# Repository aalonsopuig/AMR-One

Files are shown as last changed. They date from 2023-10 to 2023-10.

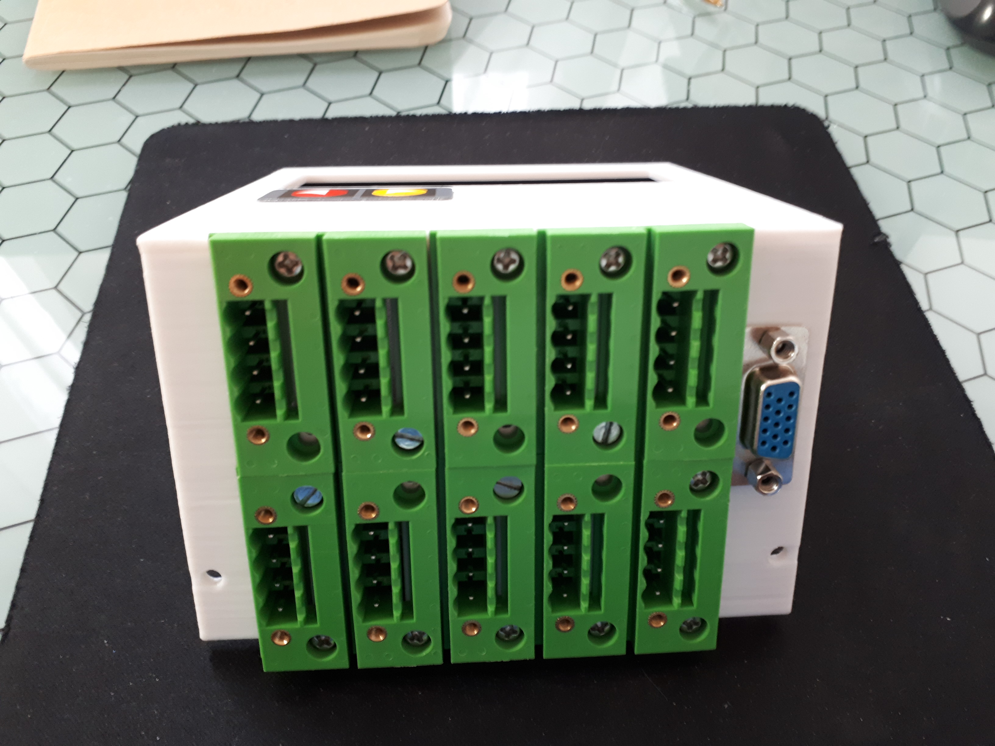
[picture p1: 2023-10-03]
amr_one_media/IMG_20210604_084052.jpg

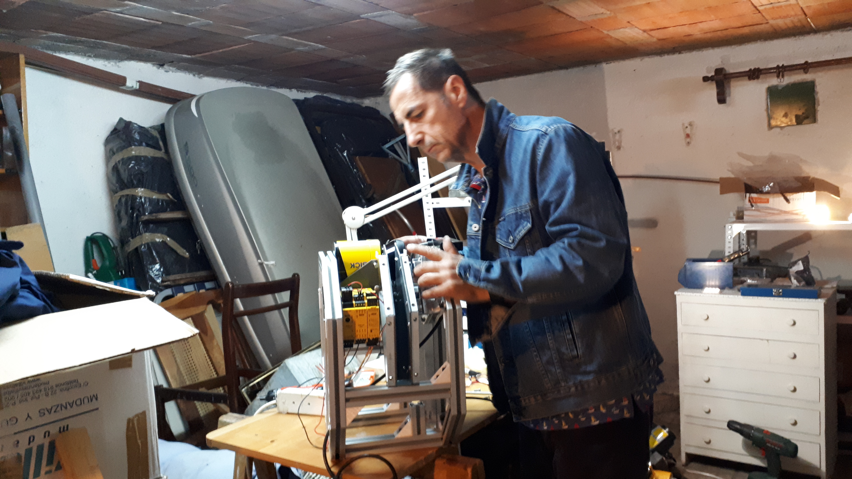
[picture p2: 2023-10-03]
amr_one_media/20200813_082543.jpg

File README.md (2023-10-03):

# AMR-One
 [C++, Python, ROS, Gcode] 2022. Autonomous Mobile Robot<br>

_Status [3/10/2023]: Done: The mechanical and electric parts of the robot, the magnetic navigation, the safety systems, and the cloud monitoring are fully operational. Pending: ROS SLAM-based navigation_
 <br><br>

## Summary of the project

The AMR-One project objective is to develop a prototype of an autonomous mobile robot for the industry, as a personal project, with some basic characteristics:<br><br>
IMG-20200915-WA0002
<br><br>
- Rotational base with damped traction system<br>
- Safety system<br>
- Pinhook system to hook trolleys from the bottom and carry them.<br>
- Two navigation modes:<br>
    * Magnetic band guidance with RFID tags control<br>
    * SLAM based navigation using ROS<br>
- Cloud monitoring (over AWS)<br><br>

## Repository content

In this repository, you could find the following folders:<br>
<br>

- **amr_one_tech_doc**: Technical documentation of the project<br>
- **amr_one_mechanical**: CAD designs produced with [FreeCad opensource program](https://www.freecad.org/), 3D printing parts, Assembly instructions, BOM,...
- **amr_one_electric**: Electric designs produced with [QElectrotech opensource program](https://qelectrotech.org/)
- **amr_one_software**: Software for Low-Level Controller (based on Arduino). Software included (.ino), Configuration of drivers, cloud,...
- **amr_one_safety**: Safety configuration for Sick FlexySoft safety PLC and Sick safety lidar
- **amr_one_media**: Photos and videos

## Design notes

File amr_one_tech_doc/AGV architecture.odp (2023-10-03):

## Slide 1

AMR Architecture

Safety

LiDAR

HMI

WIFI radio

PC

Safety PLC

Rearm button

E.Stop button

Other sensors

PLC

Magnetic band

Drives

RFID sensor

Motors

Encoders

Batt sensor

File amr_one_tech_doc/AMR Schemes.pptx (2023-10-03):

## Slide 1

Motor1_setpoint

1

PID_output1 = PID_output1 + Motor1_PID.step(Motor1_setpoint, Motor1_feedback);

Motor1_PWM = MOTORS_PWM_STOP + PID_output1;

D

Motor1_PID.step(Motor1_setpoint, Motor1_feedback);

C

6

3

Proportional

PID_output1

Motor1_PWM

FILTER

Integral

+

+

4

+

5

PWM to Volt.

Derivative

MOTORS_PWM_STOP

A

B

DRIVE

E

2

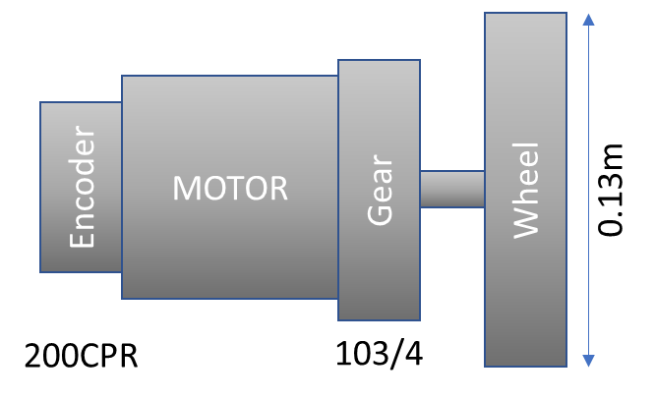
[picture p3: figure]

Motor1_feedback

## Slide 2

How 257.5 is calculated:
*
* encoder CPR: 200CPR (cycles per revolution in motor axel)
* gear ratio of motors: 103/4
* CPR_on_wheel (Resulting cycles per revolution in wheel axel): encoder CPR * gear ratio = 5150 cycles per revolution of wheel
*
* Motors_setpoint is measured in cycles of encoder per measuring time (20 miliseconds)
* period_ms = 20ms
*
* Diameter of wheel: 130mm = 13cm = 0.13m
* Perimeter_of_wheels_in_meters: Pi * Diameter = 0.4m
*
* 1 minute = 60000ms
*
* Speed_meters_per_minute = Linear_Velocity(m/s) * 60 seconds
* revolutions_per_minute = Speed_meters_per_minute / Perimeter_of_wheels_in_meters
* revolutions_per_ms = revolutions_per_minute / 60000ms
*
* Motors_setpoint = revolutions_per_ms * period_ms * CPR_on_wheel
*/

MOTOR

Encoder

Gear

Wheel

0.13m

200CPR

103/4

MOTOR

Encoder

Gear

Wheel

0.13m

200CPR

103/4

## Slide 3

MOTORS_MaxLinear_Velocity (m/s)

MOTORS_MaxAngular_Velocity x 0,836875/12.875

0

MOTORS_MaxAngular_Velocity x 0,836875/12.875

-MOTORS_MaxAngular_Velocity (rad/s)

-MOTORS_MaxLinear_Velocity (m/s)

MOTORS_MaxAngular_Velocity (rad/s)

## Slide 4

RS-232 (57.6 kBd; 8 data bits, no parity, 1 stop bit);

8C 22 0C AC xx
B9 EE F9 A9 D6

49 bits?
No empieza RS232 con high?
Debemos invertir?
Con movil da
07:46:A9:94:50:01:04:E0
Impreso: -7429-
Memoria: 1D:05

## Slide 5

RS-232 (57.6 kBd; 8 data bits, no parity, 1 stop bit);

Original Data

7.4v

0v

-8.2v

Final Data

5v

0v

Byte 1

Byte 2

Byte 3

Byte 4

Byte 5

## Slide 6

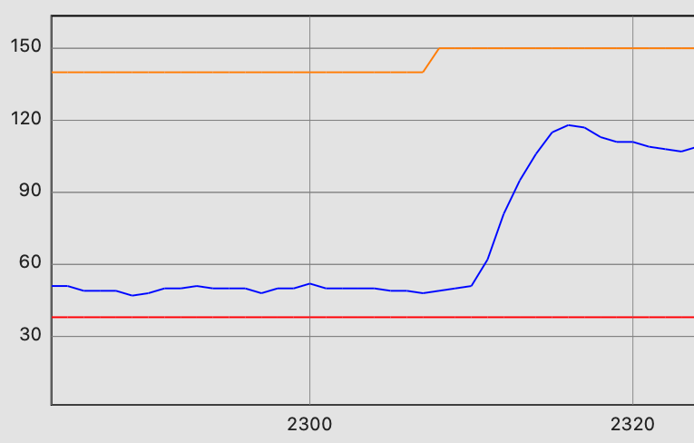
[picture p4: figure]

50ms

100ms

150ms

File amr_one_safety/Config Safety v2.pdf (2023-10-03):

# Flexi Soft Designer

# SICK

## Application name: SICK Flexi Soft main module FX3-CPU1

## Device CRC Tool: 0x3F55A961 - Device CRC Device: 0x3F55A961

## Configuration date and time: 2/8/2021 10:12:00 AM

# Flexi Soft Designer 2/8/2021 10:26:10 AM

# Content

# 1. Bill of material

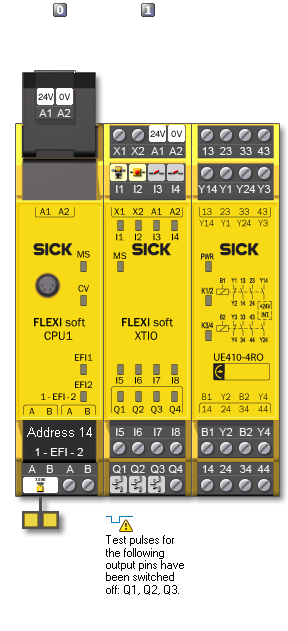
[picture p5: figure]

QTY | Title | Tag name | Part number

### Internal item number

### Description

1 | CPU1 | CPU1[0] | 1043784 | SICK Flexi Soft main module FX3-
| | | | CPU1
1 | MPL0 | System plug | 1043700 | Flexi Soft system plug
1 | S300 / Safety laser scanner, type 3 S300.CPU1
| | [0].EFI1.1 | | Sampling laser scanner for access
| | | | protection on machines, for mobile
| | | | applications as well as for vertical
| | | | access protection
1 | XTIO | XTIO[1] | 1044125 | SICK Flexi Soft expansion module
| | | | FX3-XTIO
1 | Safety switch / Single channel | Safety switch.XTIO
| | [1].I1
1 | E-Stop, ES21 / Single channel | EX-Stop.XTIO[1].I2
1 | Single channel NO / Single channel LCase1/2.XTIO[1].I3

QTY | Title | Tag name | Part number

### Internal item number

### Description

1 | Single channel NO / Single channel LCase2/2.XTIO[1].I4
1 | PNP output / Single channel | ON DRV1.XTIO
| | [1].Q1
1 | PNP output / Single channel | ON DRV2.XTIO
| | [1].Q2
1 | PNP output / Single channel | SAFETY STOP
| | ON.XTIO[1].Q3
1 | UE410-4RO3 | UE410-4RO3 | 6026143 | SICK relay output expansion
| | | | UE410-4RO3

# 2. Diagnostics

## Current operation time: 1.18:36:38, power cycle: 121 - Current: 1, Historical: 42

Time stamp | Local time | Power-up cycles Source | Code

### Description

1.18:34:07 | 2/8/2021 10:23:42 AM | 121 | Main module | 0x000F000B
Communication at EFI 1 to device address 7 interrupted: Timeout at reception of
| cyclic data. | | | [01 07 03 FFFF]
1.17:02:40 | | 120 | Extension module 1 | 0x4704
Extension module 1: cross-circuit at output Q1, 2, 3, 4 | [01 00 0F 00]
1.02:36:44 | | 104 | Extension module 1 | 0x4704
Extension module 1: cross-circuit at output Q1, 2, 4 | [01 00 0B 00]
22:55:03 | | 96 | Extension module 1 | 0x4502
Internal error: Cross-checking for inputs | [01 55 04 00]
22:55:01 | | 96 | Extension module 1 | 0x4502
Internal error: Cross-checking for inputs | [01 55 04 00]
22:54:37 | | 96 | Extension module 1 | 0x4502
Internal error: Cross-checking for inputs | [01 AA 08 00]
20:14:48 | | 80 | Extension module 1 | 0xC30A
Internal error in the Flexi Soft system. | [01 00 0F 00]
20:14:48 | | 80 | Main module | 0x0029C006
Internal error in the Flexi Soft system: Probably an extension module is
| malfunctioning. | | | [00 02 00 00]
17:51:38 | | 60 | Main module | 0x002D4006
The Flexi Soft system performed a restart due to a power supply dip at the main
| module. | | | [00 00 00 00]
14:45:52 | | 56 | Extension module 1 | 0xC30A
Internal error in the Flexi Soft system. | [01 00 0F 00]
14:45:52 | | 56 | Main module | 0x0029C006
Internal error in the Flexi Soft system: Probably an extension module is
| malfunctioning. | | | [00 02 00 00]
14:36:23 | | 46 | Main module | 0x00404006
| Force mode terminated. | | | [00 00 00 00]
14:34:12 | | 46 | Main module | 0x003F4006
| Force mode started. | | | [00 00 00 00]
14:33:44 | | 46 | Main module | 0x00404006
| Force mode terminated. | | | [00 00 00 00]
14:32:27 | | 46 | Main module | 0x003F4006
| Force mode started. | | | [00 00 00 00]
11:54:28 | | 42 | Main module | 0x00404006
| Force mode terminated. | | | [00 00 00 00]
11:52:52 | | 42 | Main module | 0x003F4006
| Force mode started. | | | [00 00 00 00]
11:05:07 | | 40 | Main module | 0x00404006
| Force mode terminated. | | | [00 00 00 00]
11:03:17 | | 40 | Main module | 0x003F4006
| Force mode started. | | | [00 00 00 00]
10:00:13 | | 39 | Main module | 0x00404006
| Force mode terminated. | | | [00 00 00 00]
09:57:58 | | 39 | Main module | 0x003F4006
| Force mode started. | | | [00 00 00 00]

Time stamp | Local time | Power-up cycles Source | Code

### Description

08:14:05 | 37 | Main module | 0x000F4013
Configuration in the system plug is incompatible for at least one extension module. [01 FFFF 00 00]
08:13:59 | 37 | Main module | 0x0019400A
Unexpected EFI device with address 7 found at EFI 1. Either remove this device or
adapt the configuration of the Flexi Soft system.

[01 07 00 00]

08:13:53 | 37 | Main module | 0x000E4006
Configuration in the system plug is invalid. | [00 00 00 01]
08:13:11 | 36 | Main module | 0x001B4005
Internal error in the Flexi Soft system. | [58E6 526D 5BF8
DB91]
07:17:20 | 28 | Main module | 0x0009400A
Communication at EFI1 interrupted. Communication driver has switched off. After
solving the fault a restart of the Flexi Soft system is necessary.

[01 422 00 00]

06:51:21 | 28 | Main module | 0x000F4013
Configuration in the system plug is incompatible for at least one extension module. [01 FFFF 00 00]
06:51:15 | 28 | Main module | 0x0019400A
Unexpected EFI device with address 7 found at EFI 1. Either remove this device or
adapt the configuration of the Flexi Soft system.

[01 07 00 00]

06:51:09 | 28 | Main module | 0x000E4006
Configuration in the system plug is invalid. | [00 00 00 01]
06:50:56 | 27 | Main module | 0x001B4005
Internal error in the Flexi Soft system. | [5DB5 A17E 5EAB
2882]
06:47:07 | 27 | Main module | 0x001B4005
Internal error in the Flexi Soft system. | [5DB5 A17E 5EAB
2882]
05:11:53 | 20 | Extension module 1 | 0x4704
Extension module 1: cross-circuit at output Q1, 2, 3, 4 | [01 00 0F 00]
04:50:54 | 18 | Main module | 0x0019400A
Unexpected EFI device with address 7 found at EFI 1. Either remove this device or
adapt the configuration of the Flexi Soft system.

[01 07 00 00]

02:15:25 | 11 | Main module | 0x0019400A
Unexpected EFI device with address 7 found at EFI 1. Either remove this device or adapt the configuration of the Flexi Soft system.

[01 07 00 00]

02:13:12 | 10 | Main module | 0x00404006
Force mode terminated. | [00 00 00 00]
02:11:32 | 10 | Main module | 0x003F4006
Force mode started. | [00 00 00 00]
02:01:45 | 10 | Main module | 0x000F4013
Configuration in the system plug is incompatible for at least one extension module. [01 FFFF 00 00]
02:01:33 | 10 | Main module | 0x000E4006
Configuration in the system plug is invalid. | [00 00 00 01]
02:01:00 | 9 | Main module | 0x000F4013
Configuration in the system plug is incompatible for at least one extension module. [01 FFFF 00 00]
02:00:48 | 9 | Main module | 0x000E4006
Configuration in the system plug is invalid. | [00 00 00 01]
01:57:38 | 8 | Main module | 0x000F4013
Configuration in the system plug is incompatible for at least one extension module. [01 FFFF 00 00]
01:57:26 | 8 | Main module | 0x000E4006
Configuration in the system plug is invalid. | [00 00 00 01]
01:55:17 | 7 | Extension module 1 | 0x4601
Extension module 1: Cross circuit at input I1 | [01 00 01 00]

# 3. Summary

# 3.1. Module 0

### Device class:

### Type code: Serial number:

### Software version

### Hardware version:

### Version/ Step:

### Operational status:

CPU1 | FX3-
CPU130002
1427 0089 | V 3.01.0 | 4.00 | 1.9.2.187 V 3.xx Online

# 3.2. Module 1

### Device class:

### Type code: Serial number:

### Software version

### Hardware version:

### Version/ Step:

### Operational status:

XTIO | FX3-XTIO84002 1632 1341 | V 3.10.0 | 1.11 | 1.9.2.187 V 3.xx Online

# 3.3. EFI 1.1 S300 [H]

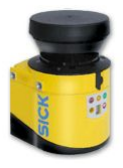
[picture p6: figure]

Device | S300 [H]
Device name | S300 LR
Type code | S30B-3011GB
Serial number | 19250478
| 15391838
Software version | 02.11
Operational status | Online

# 4. Configuration

# 4.1. Installed software components

Basic components (station) | 1.9.2.187
Software component for GCC1 Network Modules | 1.9.1.279
Software component for GS3S gateway | 1.8.0.1
Software component for UE410-2RO3 relay module | 1.9.2.187
Software component for UE410-4RO3 relay module | 1.9.2.187
Software components for Flexi-Soft FX3-ANA0 expansion module 1.9.2.187
Software component for GCAN gateway | 1.9.2.187
Software component for GDEV gateway | 1.9.2.187
Software component for GENT gateway | 1.9.2.187
Software component for GETC gateway | 1.9.2.187
Software component for GMOD gateway | 1.9.2.187
Software component for GPNT gateway | 1.9.2.187
Software component for GPRO gateway | 1.9.2.187
Software component for Drive Monitor FX3-MOC0 module | 1.9.2.187
Software component for Drive Monitor FX3-MOC1 module | 1.9.2.187
Software components for MOC3SA Motion Control module | 1.9.2.187

Software component for ReLy OSSD4 relay module | 1.9.2.187
Software component for STIO expansion module | 1.9.2.187
Software component for UE10 relay module | 1.9.2.187
Software component for UE12 relay module | 1.9.2.187
Software component for XTDI extension module | 1.9.2.187
Software components for FX3-XTDS expansion module | 1.9.2.187
Software component for XTIO extension module | 1.9.2.187
Software component for CPU0 and CPU1 main modules | 1.9.2.187

# 4.2. General information

User group | Authorized client
Application name | SICK Flexi Soft main module FX3-CPU1
Application description
Configuration CRC | 0x3F55A961
Device CRC | 0x3F55A961
Configuration state | Verified
Device state | Verified
Configuration date | 2/8/2021 10:12 AM

Module | Type code | Step | Address
CPU1 | FX3-CPU130002 | V 3.xx | 0
XTIO | FX3-XTIO84002 | V 3.xx | 1
UE410-4RO3 | UE410-4RO3 | -

# 4.3. CPU

## 4.3.1. CPU1 - General information

### Type code Serial number

| Software
| version | Hardware
| | version | Version/Step Memory
| | | usage (UI/
| | | Logic)

### Address

FX3-CPU130002 1427 0089 | V 3.01.0 | 4.00 | 1.9.2.187 V 3.xx 6.14% / 6.01% | 0
FX3-MPL000001 1435 0415 | - | - | 1.9.2.187 | - | -
S30B-3011GB | - | - | - | - | - | EFI1.1

## 4.3.1.1. CRC values

### Project CRC value

### Device CRC value

Configuration CRC | 0x3F55A961 | 0x3F55A961

## 4.3.2. CPU logic

### Used

Function blocks | 15
Execution time (ms) | 4

## 4.3.2.1. 0-Inputs

No Name | Input | Output | Settings
0 | Routing N:N I.0 LCase1/2.XTIO[1].I3 | O.0 Routing 1:N 0 -> I.0 ->
Input
| | | | Input 1: Not Inverted
| | I.1 LCase2/2.XTIO[1].I4 | O.1 Routing 1:N 2 -> I.0 ->
Input
| | | | Input 2: Not Inverted
| | I.2 EX-Stop.XTIO[1].I2 | O.2 Routing N:N 0 -> I.2 ->
Input 3
| | | | Input 3: Inverted
5 | Routing N:N I.0 Protective field free
| | [SF].CPU1[0].EFI1.1 | O.0 Routing N:N 0 -> I.0 ->
Input 1
| | | | Input 1: Inverted
6 | Emergency
stop | | I.0 Safety switch.XTIO
[1].I1
| | | O.0 Routing N:N 0 -> I.1 ->
Input 2

Inputs: Single channel

Discrepancy time: 30 ms
Mode: Emergency stop

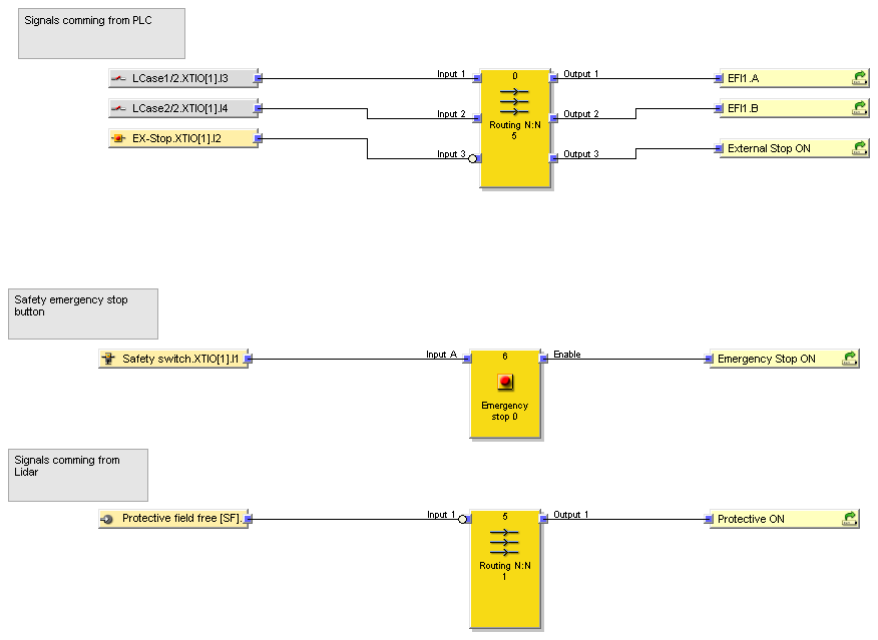
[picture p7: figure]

## 4.3.2.2. Outputs

No Name | Input | Output | Settings
1 | Routing 1:N I.0 Routing N:N 5 -> O.0 ->
| Output 1 | O.0 Input A2 [In A2].CPU1 [0].EFI1.1 O.1 NOT 0 -> I.0 -> Input
2 | NOT | I.0 Routing 1:N 0 -> O.1 ->
| Output 2 | O.0 Input A1 [In A1].CPU1 [0].EFI1.1
3 | Routing 1:N I.0 Routing N:N 5 -> O.1 ->
| Output 2 | O.0 Input B2 [In B2].CPU1 [0].EFI1.1 O.1 NOT 1 -> I.0 -> Input
4 | NOT | I.0 Routing 1:N 2 -> O.1 ->
| Output 2 | O.0 Input B1 [In B1].CPU1 [0].EFI1.1
7 | Routing N:N I.0 Routing N:N 1 -> O.0 ->
| Output 1

O.0 OR 0 -> I.0 -> Input 1 Input 1: Not Inverted

| I.1 Emergency stop 0 -> O. 0 -> Enable

O.1 OR 0 -> I.1 -> Input 2 Input 2: Not Inverted

| I.2 Routing N:N 5 -> O.2 -> Output 3

O.2 OR 1 -> I.1 -> Input 2 Input 3: Not Inverted

8 | OR | I.0 Routing N:N 0 -> O.0 ->
| Output 1 | O.0 Off delay timer 0 -> I.0 -> Input | Input 1: Not Inverted
| I.1 Routing N:N 0 -> O.1 -> Output 2 | | Input 2: Not Inverted
9 | Off delay
timer

I.0 OR 0 -> O.0 -> Output 1 O.0 Routing 1:N 3 -> I.0 ->

| | Input | Delay time: 2000 ms
10 | Routing 1:N I.0 Off delay timer 0 -> O.0
| -> Enable | O.0 SAFETY STOP ON.XTIO[1].Q3 O.1 OR 1 -> I.0 -> Input 1
11 | OR | I.0 Routing 1:N 3 -> O.1 ->
| Output 2 | O.0 Routing 1:N 1 -> I.0 -> Input | Input 1: Not Inverted
| I.1 Routing N:N 0 -> O.2 -> Output 3 | | Input 2: Not Inverted
12 | Routing 1:N I.0 OR 1 -> O.0 -> Output 1 O.0 NOT 2 -> I.0 -> Input
| | O.1 NOT 3 -> I.0 -> Input
13 | NOT | I.0 Routing 1:N 1 -> O.0 ->
| Output 1 | O.0 ON DRV1.XTIO[1].Q1
14 | NOT | I.0 Routing 1:N 1 -> O.1 ->
| Output 2 | O.0 ON DRV2.XTIO[1].Q2

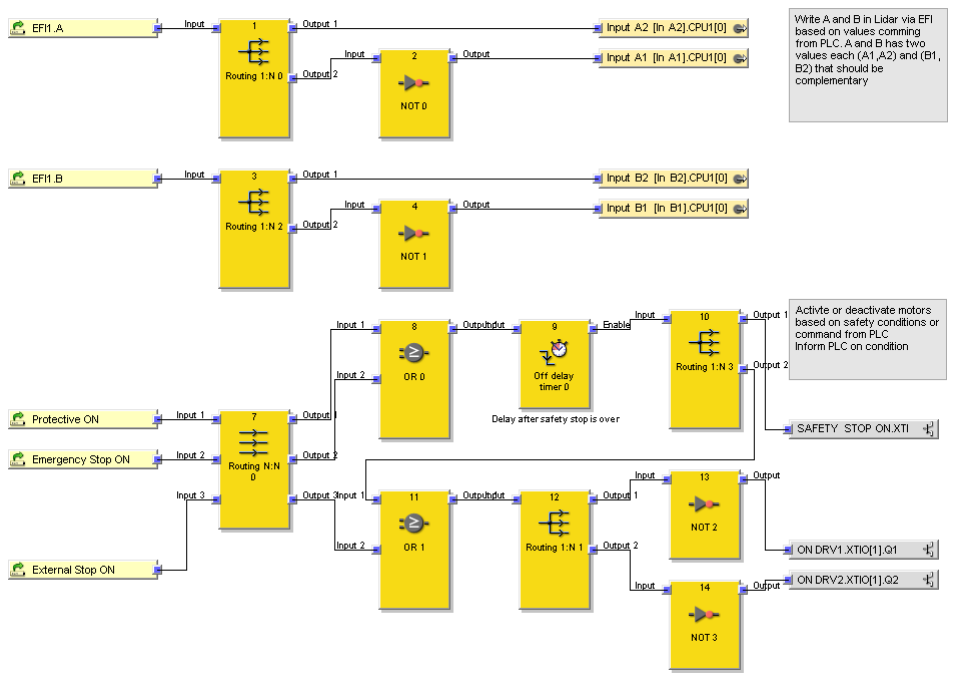
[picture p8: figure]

## 4.3.3. CPU1 - IO

Tag name | System integrity

### test based on type key

### System integrity test based on serial number

### System integrity test based on configuration date

24V | A1 | CPU1[0] Power supply
0V | A2
EFI1.1 S300.CPU1[0].EFI1.1

## 4.3.3.1. Wiring diagram

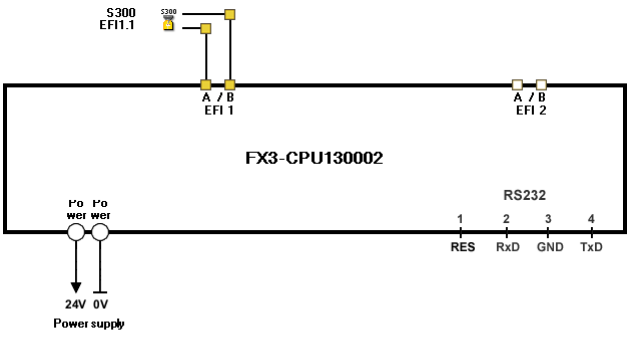
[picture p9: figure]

# 4.4. I/O module

## 4.4.1. XTIO[1]

## 4.4.1.1. General information

### Type code Serial number

### Software version

### Hardware version

### Version/Step Address

FX3-XTIO84002 1632 1341 | V 3.10.0 | 1.11 | 1.9.2.187 V 3.xx 1

## 4.4.1.2. Inputs

Mode | Title/tag name | ON-

### OFF

### OFF-

ON

### Filter time

[ms]

Dis.
[ms]

### Test period

[ms]

### Test gap

[ms]

### Max. off-on delay

[ms]
2 | 24V | I1 | Safety switch (Single
channel)
8 | – | – | – | –
3 | 24V | I2 | E-Stop, ES21 (Single
channel) / EX-Stop
0 | – | – | – | –

Mode | Title/tag name | ON-

### OFF

### OFF-

ON

### Filter time

[ms]

Dis.
[ms]

### Test period

[ms]

### Test gap

[ms]

### Max. off-on delay

[ms]
4 | 24V | I3 | Single channel NO (Single
channel) / LCase1/2
0 | – | – | – | –
5 | 24V | I4 | Single channel NO (Single
channel) / LCase2/2
0 | – | – | – | –

## 4.4.1.3. Outputs

Mode | Title/tag name | Test

### pulse

### Increase

d

### capaciti ve loads

6 | Q1 | PNP output (Single channel) / ON DRV1 | Without | Disabled
7 | Q2 | PNP output (Single channel) / ON DRV2 | Without | Disabled
8 | Q3 | PNP output (Single channel) / SAFETY STOP ON | Without | Disabled

## 4.4.1.4. Power supply

### Title/tag name

1 24V
0V

A1
A2

XTIO[1] Power supply

## 4.4.1.5. Wiring diagram

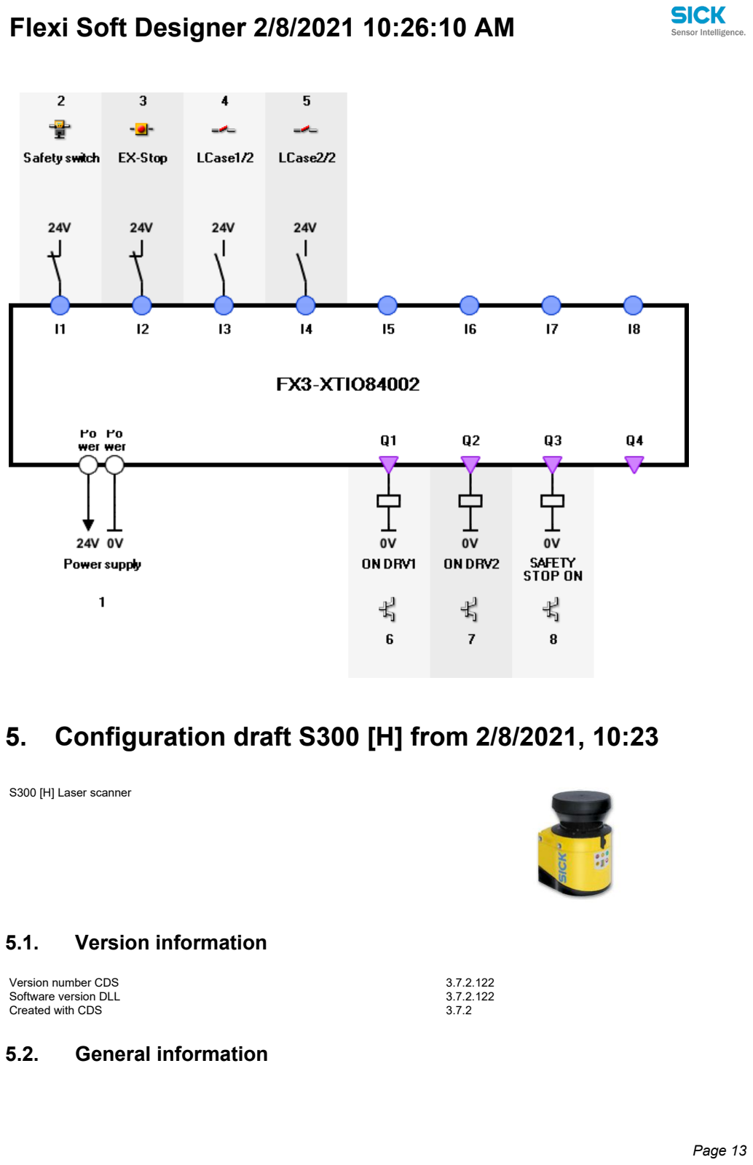
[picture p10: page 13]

# 5. Configuration draft S300 [H] from 2/8/2021, 10:23

S300 [H] Laser scanner

# 5.1. Version information

Version number CDS | 3.7.2.122
Software version DLL | 3.7.2.122
Created with CDS | 3.7.2

# 5.2. General information

Type code | S30B-3011GB
Device name | S300 LR
Serial number | 19250478
Serial number (Scanner) | 19250478
Serial number (System plug) | 15391838
Software version (CPU A) | 02.11
Software version (CPU B) | 02.11
Sensor head | Long Range (3.0 m)
I/O module
Safety Configuration ID (SCID) | 0x9C90
Status | checked

# 5.3. System parameters

Name of the user | AAP
Application name | None
Rotation of the 7segment display | Rotated by 180°

# 5.4. Resolution/scanning range

Application variant | Mobile
Resolution protective field | 70 mm (leg detection)
Basic response time | 80 ms
Maximum protective field range | 300 cm
Angular resolution | 0.5 °

# 5.5. Incremental encoder

Signal velocities | Inactive

# 5.6. Inputs

## Control inputs (Permanently)

Input source | CPU1
Input delay | 10 ms
Sampling for the static control inputs | Complementary
A | Active
B | Active
C | Inactive
D | Inactive
E | Inactive

# 5.7. OSSDs

Object in the protective field switches OSSDs | Local
External device monitoring | Inactive

# 5.8. Restart

Restart internal OSSDs | Delay by 2 s

# 5.9. Universal I/O

### Uni I/O 1 (Pin5)

### Uni I/O 2 (Pin6)

### Uni I/O 3 (Pin13)

### Uni I/O 4 (Pin14)

### Uni I/O 5 (Pin15)

### Inputs

External device monitoring | - | x
Reset | x | -

### Outputs

Contamination warning | x | - | -
Contamination error | x | - | -
Reset required | - | - | -
Error | - | - | -
Protective field | - | - | x
Warning field 1 | - | x | -
Warning field 2 | - | x | -

# 5.10. Configuration of the measured data output

Baud rate | 500 kBaud
Silent Time | 5000ms
Send mode | Continuous data output
Trigger event | Inactive
Measured data output | Distance
I/O data output | Current monitoring case
Message structure | 1 message (I/O + measured data)
Measuring range(s) | Beginning [°] | End [°] | Type
Measuring range 1 | -45 | 225 | Every value

# 5.11. Cases

Number of monitoring cases | | 4

## 5.11.1. Monitoring case 1

Monitoring case name | | Short Case
Park mode | | Inactive
Allocated field set | | Short Fields
Multiple sampling | | 4

## Activation of the inputs

Control input A | Low level
Control input B | Low level
Velocity range | Inactive

## Switching sequence

Following case | Any

## 5.11.2. Monitoring case 2

Monitoring case name | Long Case
Park mode | Inactive
Allocated field set | Long Fields
Multiple sampling | 4

## Activation of the inputs

Control input A | Low level
Control input B | High level
Velocity range | Inactive

## Switching sequence

Following case | Any

## 5.11.3. Monitoring case 3

Monitoring case name | No detection
Park mode | Inactive
Allocated field set | No detection
Multiple sampling | 2

## Activation of the inputs

Control input A | High level
Control input B | High level
Velocity range | Inactive

## Switching sequence

Following case | Any

## 5.11.4. Monitoring case 4

Monitoring case name | Park mode
Park mode | Active

## Activation of the inputs

Control input A | High level
Control input B | Low level
Velocity range | Inactive

## Switching sequence

Following case | Any

# 5.12. Field sets

Number of field sets | 3

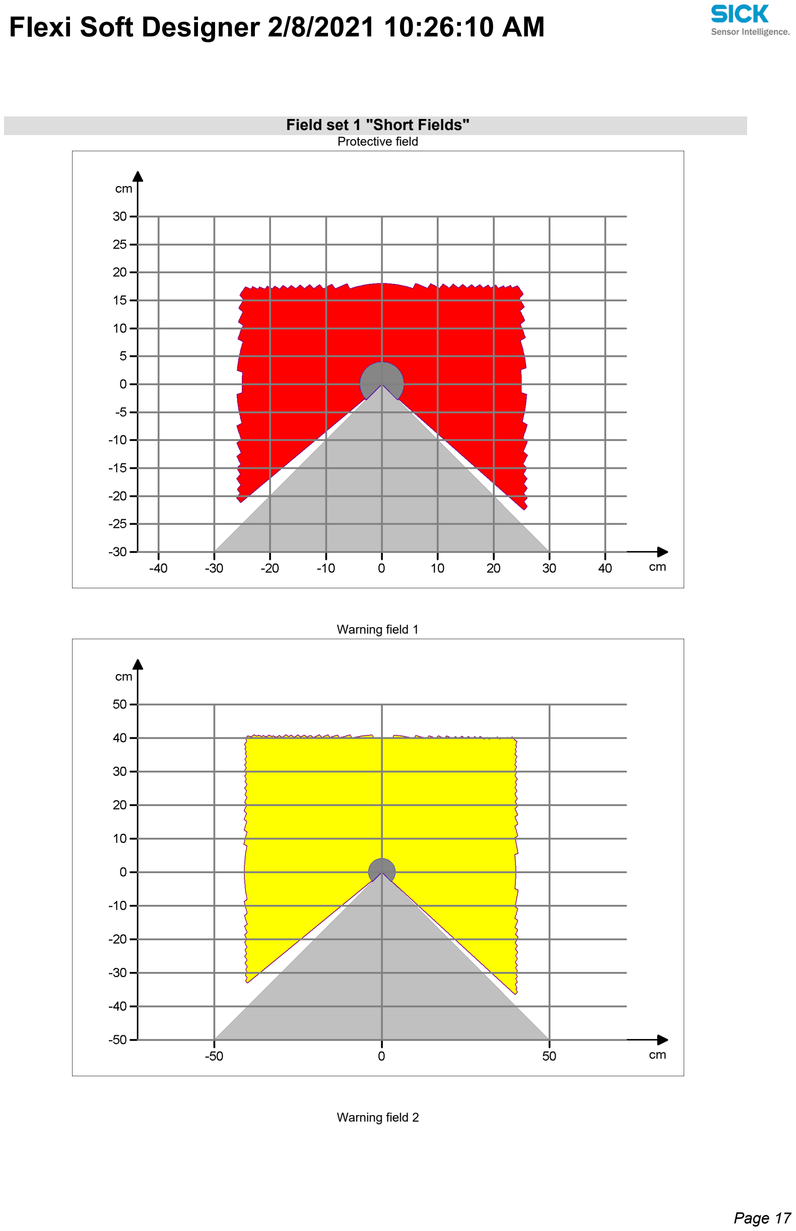
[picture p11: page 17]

### Field set 1 "Short Fields"

Protective field

Warning field 1

Warning field 2

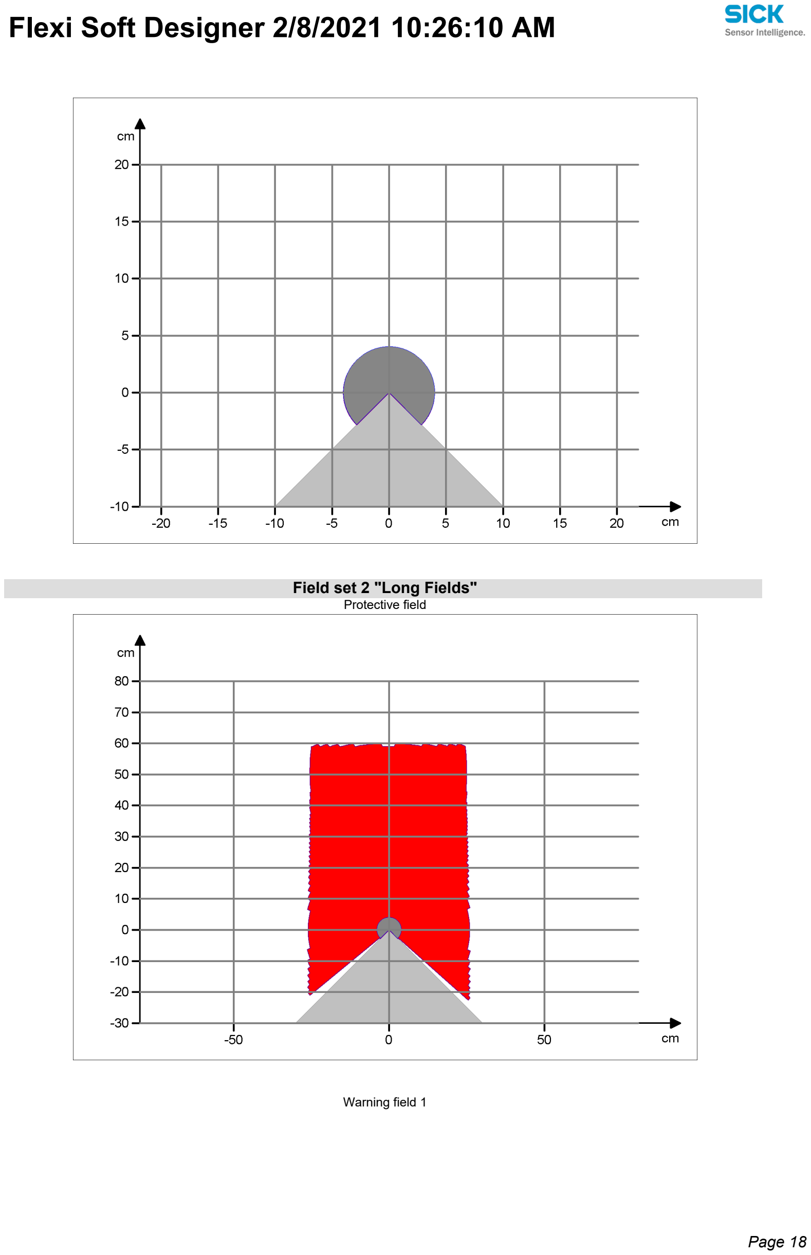
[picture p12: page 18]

### Field set 2 "Long Fields"

Protective field

Warning field 1

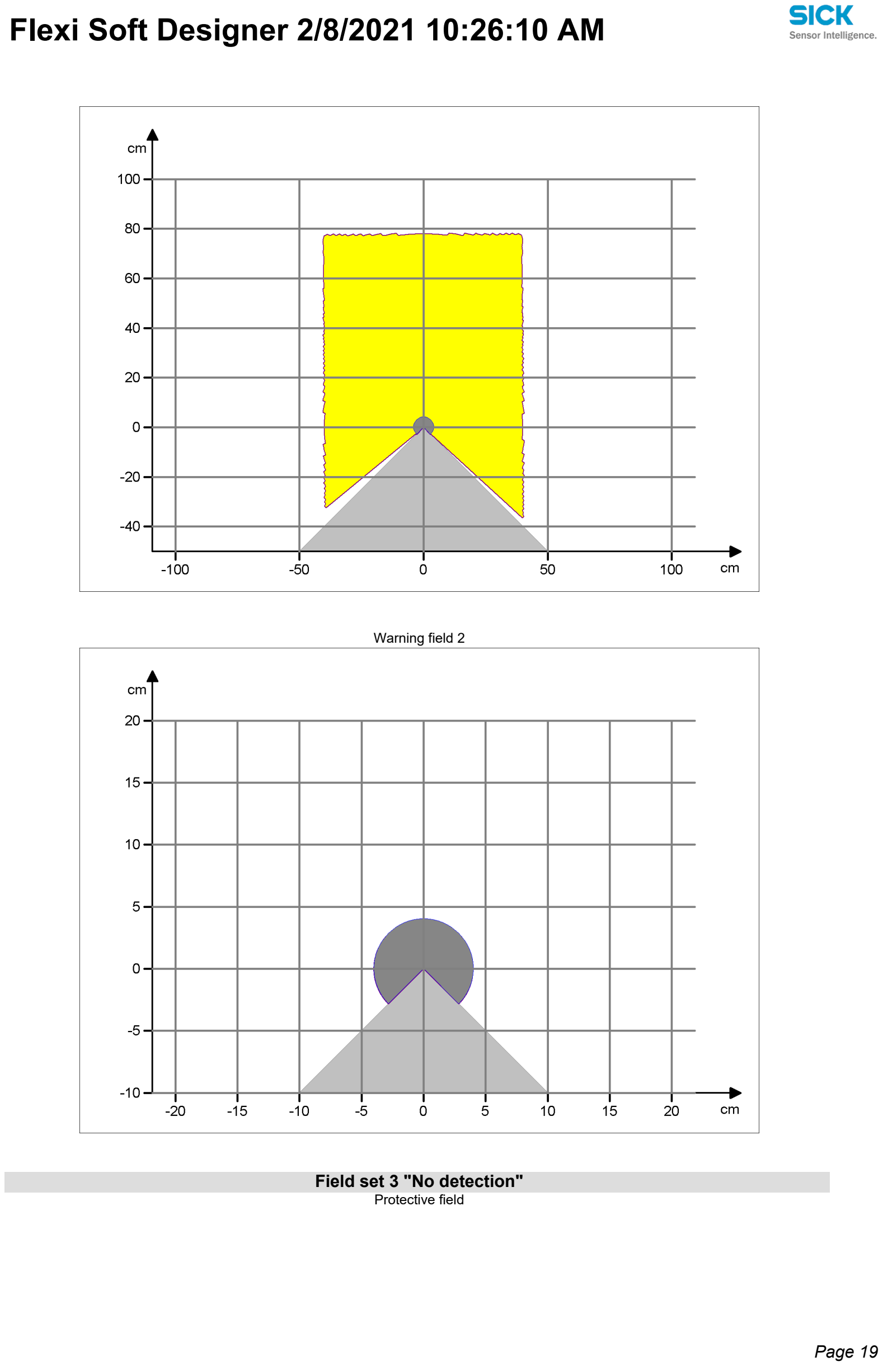
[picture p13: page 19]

Warning field 2

### Field set 3 "No detection"

Protective field

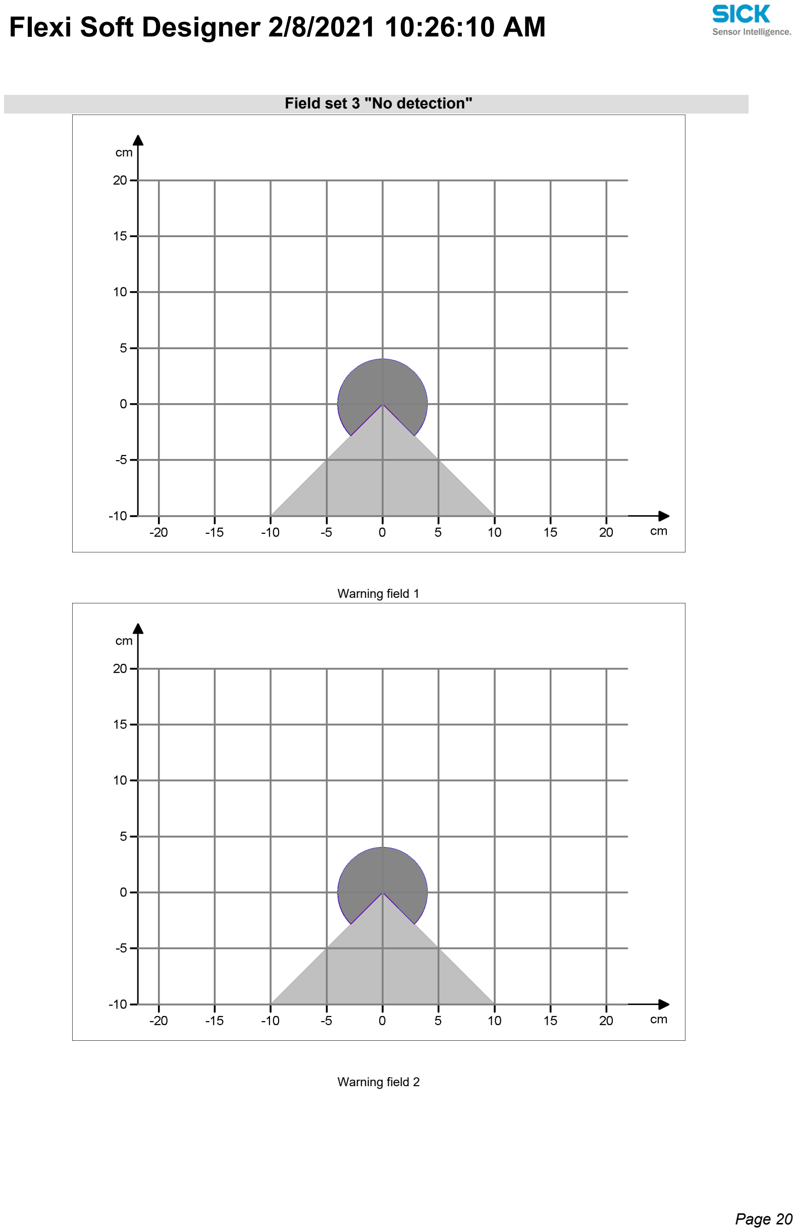
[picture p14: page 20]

### Field set 3 "No detection"

Warning field 1

Warning field 2

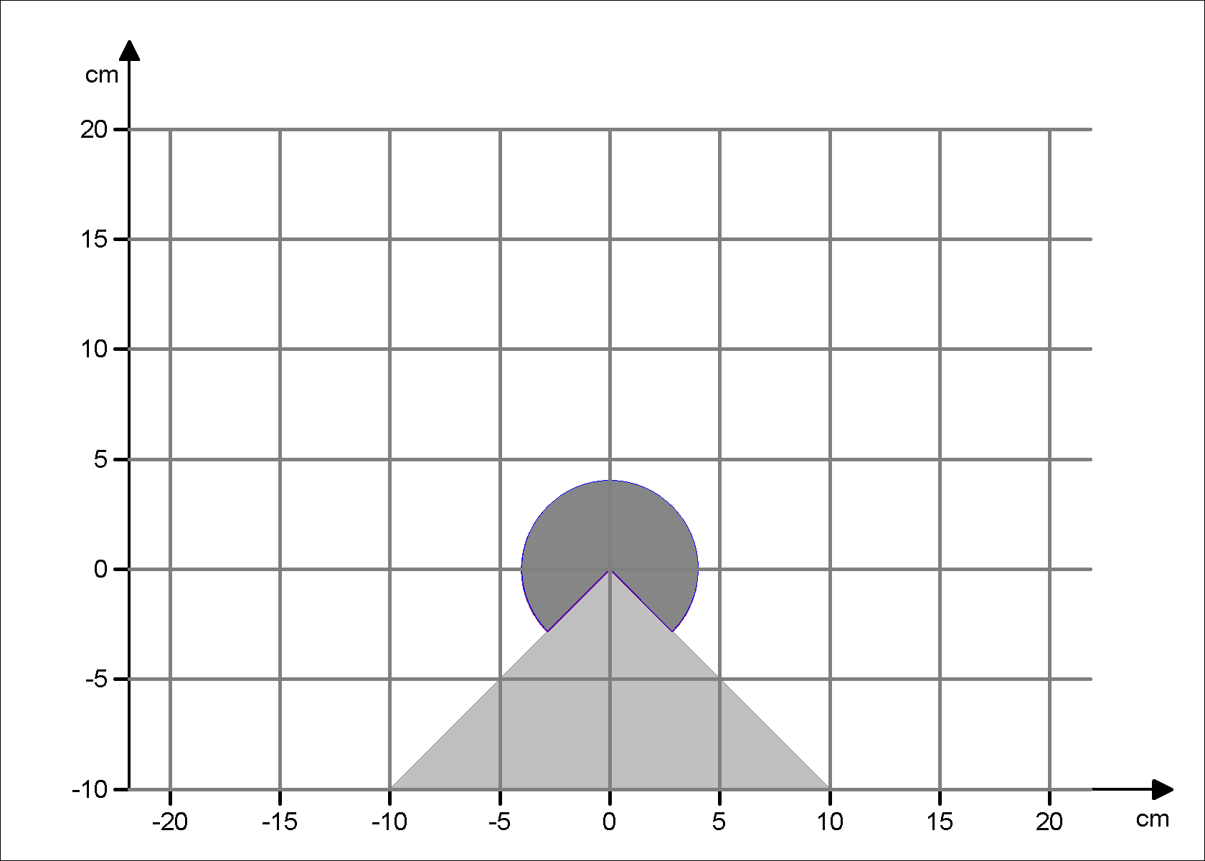
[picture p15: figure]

# 6. I/O overview

# 6.1. I/O module

XTIO[1] | Safety
switch.XTIO
[1].I1
0-Inputs | FB6 Emergency stop Input A

ON
DRV1.XTIO
[1].Q1
Outputs | FB13 NOT Output

EX-Stop.XTIO
[1].I2
0-Inputs | FB0 Routing N:N Input 3

ON
DRV2.XTIO
[1].Q2
Outputs | FB14 NOT Output

LCase1/2.XTI
O[1].I3
0-Inputs | FB0 Routing N:N Input 1

SAFETY
STOP
ON.XTIO
[1].Q3
Outputs | FB10 Routing 1:N Output 1

LCase2/2.XTI
O[1].I4
0-Inputs | FB0 Routing N:N Input 2

S300 [H]
[EFI1.1]

Input A1 [In
A1].CPU1
[0].EFI1.1
Outputs | FB2 NOT Output

Input A2 [In
A2].CPU1
[0].EFI1.1
Outputs | FB1 Routing 1:N Output 1

Input B1 [In
B1].CPU1
[0].EFI1.1
Outputs | FB4 NOT Output

Input B2 [In
B2].CPU1
[0].EFI1.1
Outputs | FB3 Routing 1:N Output 1

Protective field
free [SF].CPU1
[0].EFI1.1
0-Inputs | FB5 Routing N:N Input 1

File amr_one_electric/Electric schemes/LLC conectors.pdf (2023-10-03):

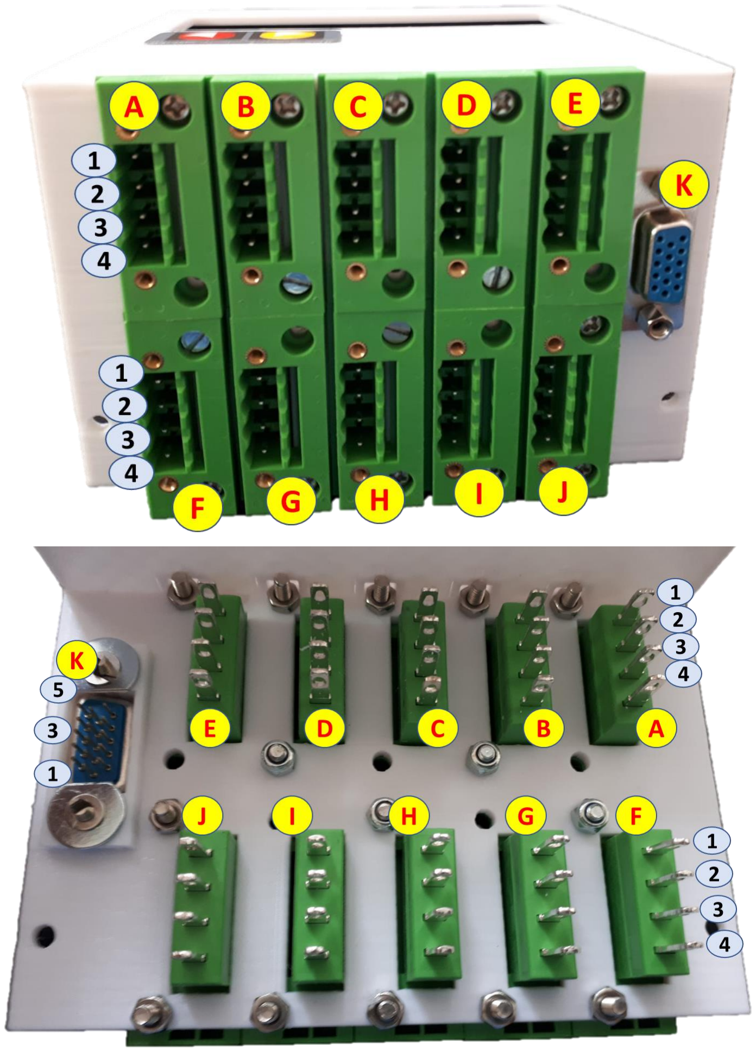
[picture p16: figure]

A. LIDAR
1. White. Lidar_Protect
2. Yellow. Lidar_Warning
3. Brown. Lidar_Dirty
4. Green. Lidar_Reset
B. Unasigned
1.
2.
3.
4.
C. SERIAL HLC
1. Black.

–LLCtrl (5v)
2. Orange. TX0

-PC
3. Gray. RX0

-PC
4.
D. Motor drive + Pinhook
1. Brown. Pinhook_a
2. White. Pinhook_b
3. Pink. Motor1_Pwm
4. Green. Motor2_Pwm
E. Button
1. Yellow. Pin_Button_Led
2. Black.

–LLCtrl (5v)
3. White. Pin_ Button
4. Red. +LLCtrl (5v)
F. POWER
1. Orange. +LLCtrl (24v)
2. Gray.

–LLCtrl (24v)
3. Red. +LLCtrl (5v)
4. Black.

–LLCtrl (5v)
G. MAG Sensor
1. Blue. MSel1
2. Yellow. MSel2
3. White. MDev
4. Brown. MGate
H. Encoder 1
1. Yellow. Encoder 1A
2. Green. Encoder 1B
3. Red. +LLCtrl (5v)
4. Black.

–LLCtrl (5v)
I. Encoder 2
1. Yellow. Encoder 1A
2. Green. Encoder 1B
3. Red. +LLCtrl (5v)
4. Black.

–LLCtrl (5v)
J. Flexi
1. Blue. SafetyStop
2. Brown. Motors_Stop
3. White. Lidar_CaseBit0
4. Yellow. Lidar_CaseBit1
K. RFID interrogator
1. Orange. +LLCtrl (24v)
3. Purple. RFID TX
5. Gray.

–LLCtrl (24v)

# LLC Connectors

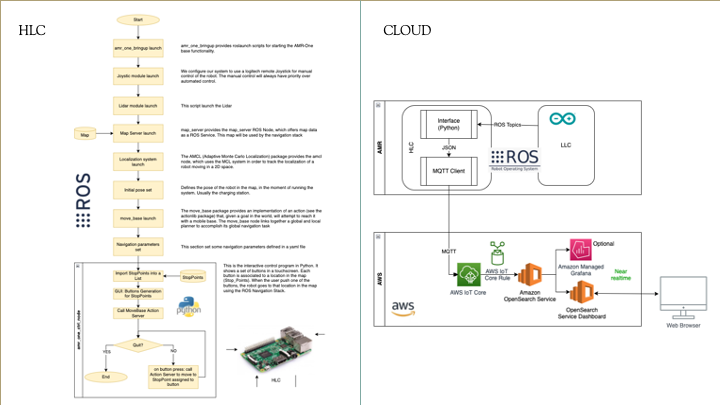
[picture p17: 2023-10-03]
amr_one_software/SW Architecture/arch_hlc_cloud.png

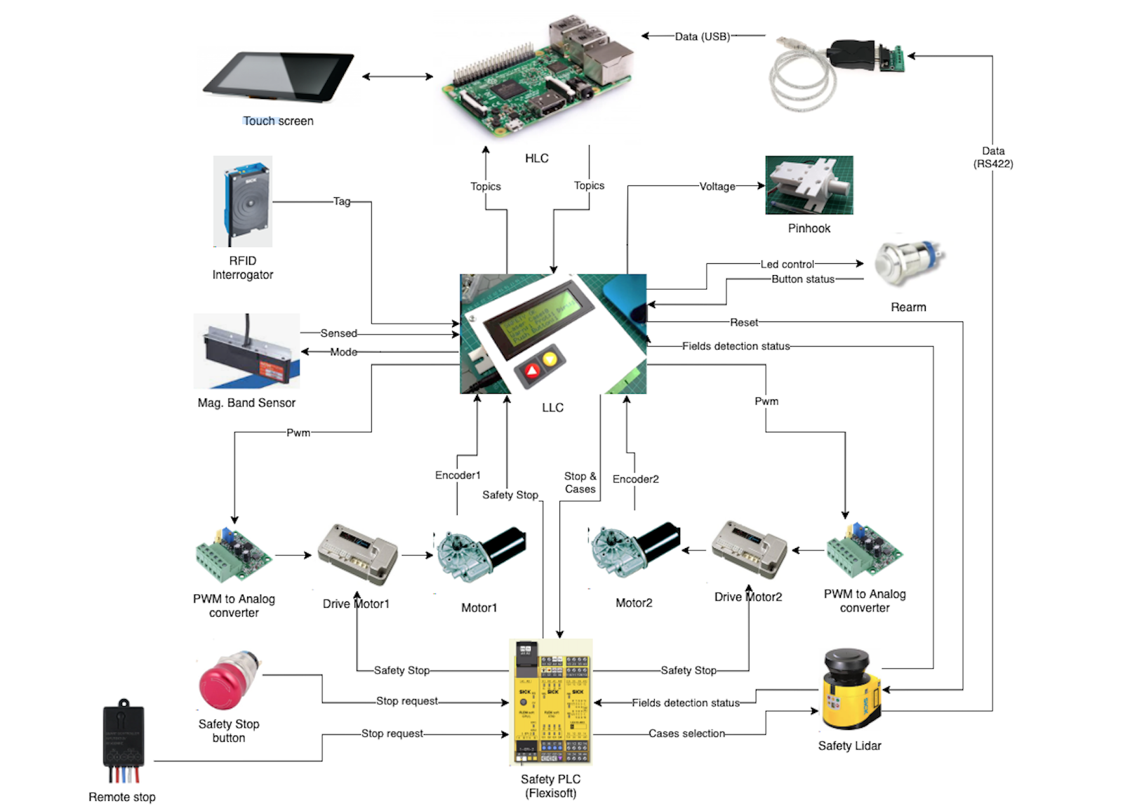
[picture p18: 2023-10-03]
amr_one_electric/HW architecture.png

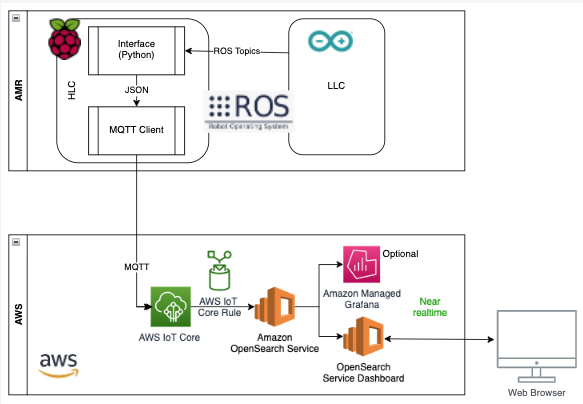
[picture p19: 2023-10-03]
amr_one_software/SW Architecture/Core Rue.png

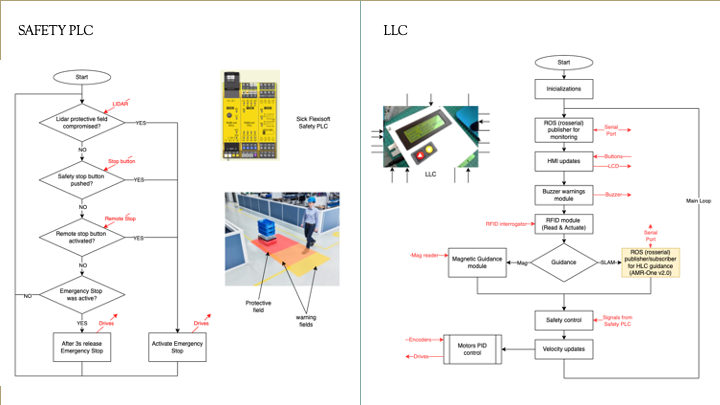
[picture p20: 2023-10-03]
amr_one_software/SW Architecture/Software.png

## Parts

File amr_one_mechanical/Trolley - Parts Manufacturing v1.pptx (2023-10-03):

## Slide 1

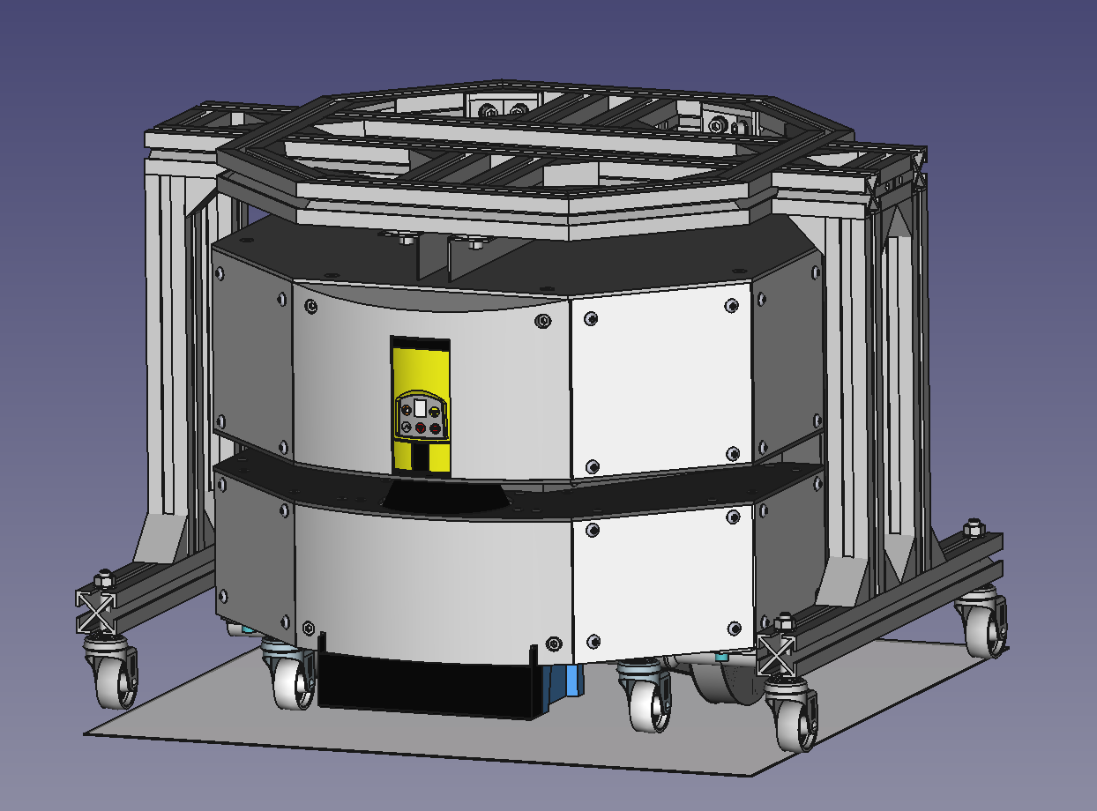
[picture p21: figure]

Trolley
Parts manufacturing

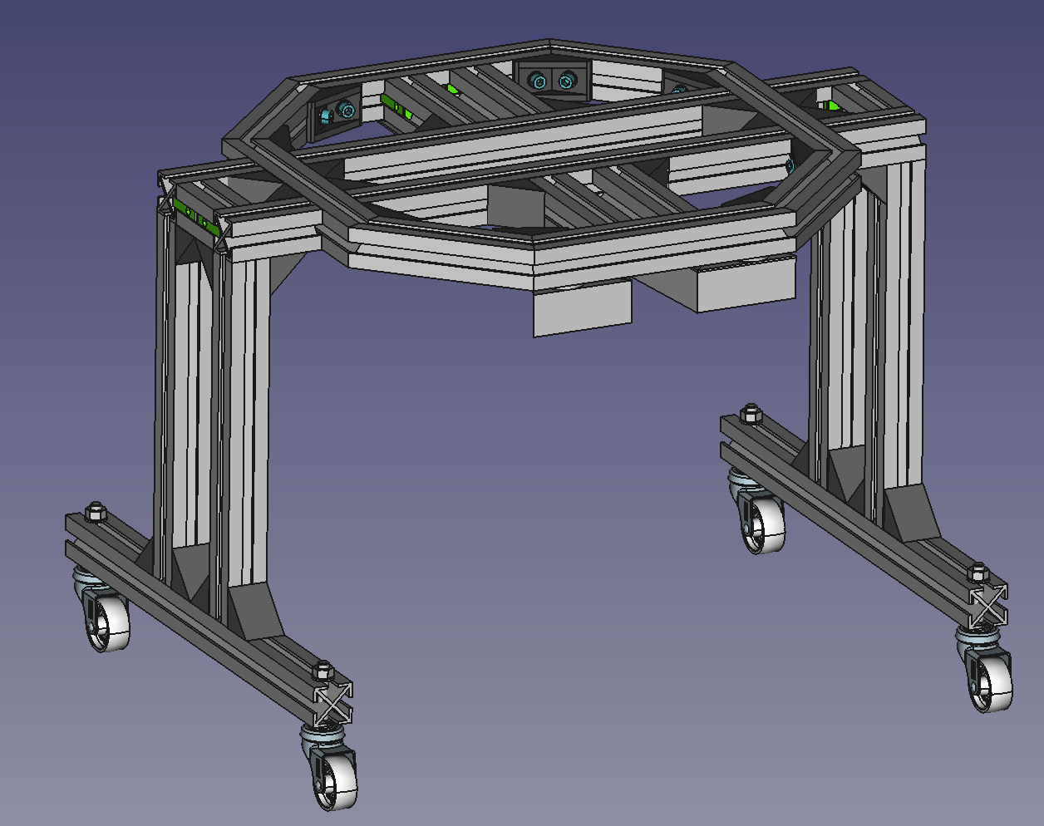
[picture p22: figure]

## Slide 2

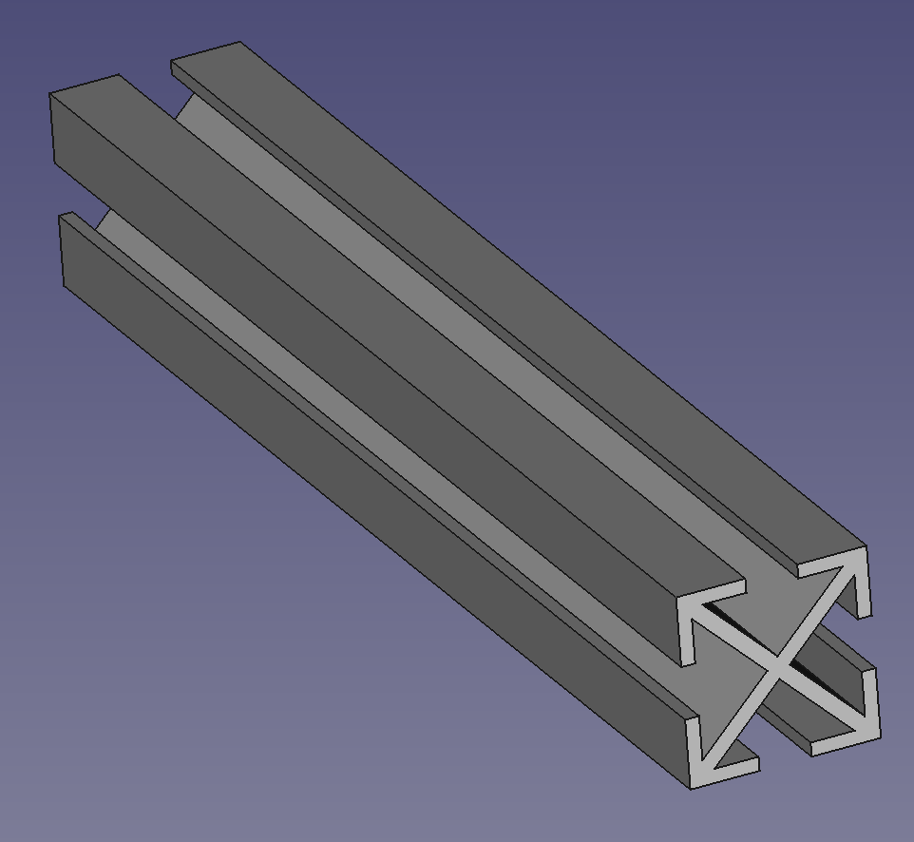
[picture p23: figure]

NOTE P176: In the each unit make two 8,2mm hole at 20mm from edge for caster wheels

P0156 | 30x30_109 mm profile flat cut | Units: 4, Assembly: Base
P0171 | 30x30_339mm profile flat cut | Units: 2, Assembly: Base
P0176 | 31x30_400mm profile flat cut | Units: 1+1, Assembly: Leg-Right, Leg-Left
P0177 | 32x30_271mm profile flat cut | Units: 2+2, Assembly: Leg-Right, Leg-Left
P0175 | 30x30_60mm profile flat cut | Units: 1+1, Assembly: LegSupport-Right / Left
P0178 | 30x30_70mm profile flat cut | Units: 2+2, Assembly: LegSupport-Right / Left

Source model for all: “30x30 profile” / 30x30 profiles.FCStd

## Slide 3

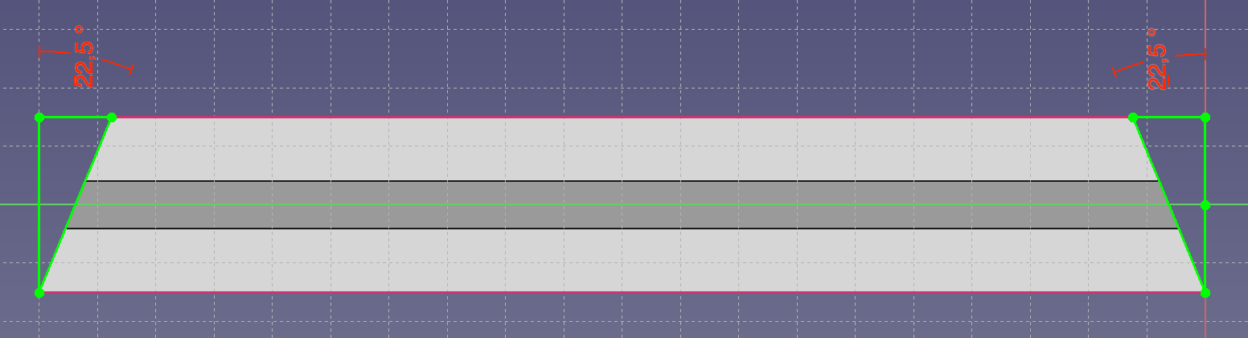
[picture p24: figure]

Length long side: 204mm
Cut angle: 22,5deg both sides
Units: 4
Assembly: Base

Length long side: 138mm
Cut angle: 22,5deg both sides
Units: 4
Assembly: Base

P0160 | 30x30 204mm profile 22,5deg cut

P0165 | 30x30 138mm profile 22,5deg cut

Source model for all: “30x30 profile” / 30x30 profiles.FCStd

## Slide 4

P0381 | Anchorage base sheet
P0391 | Steel trigger

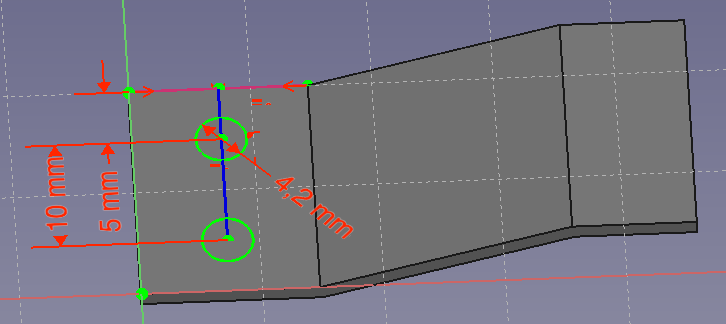
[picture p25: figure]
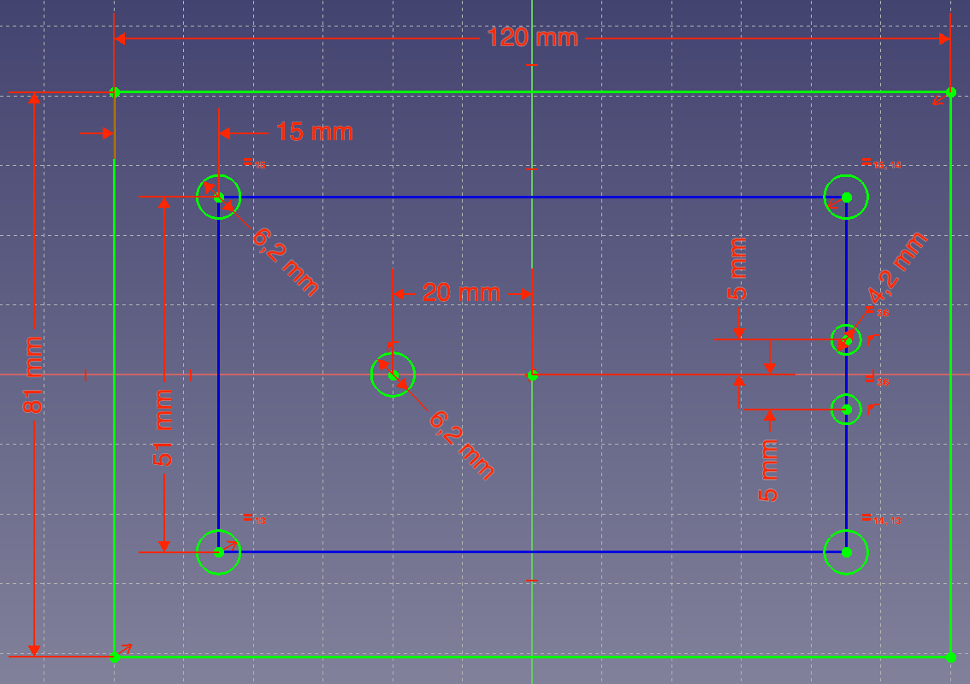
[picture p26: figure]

20mm width, 47mm length

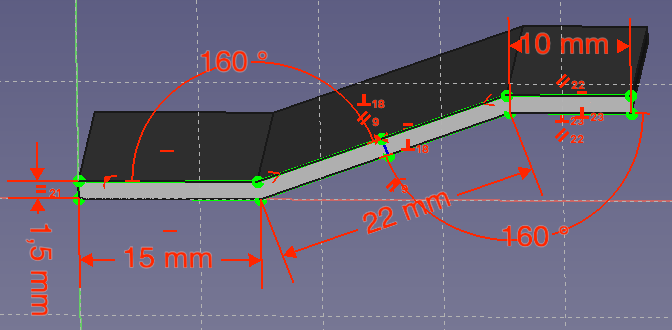
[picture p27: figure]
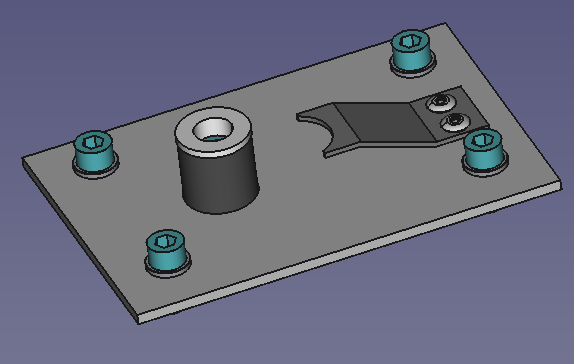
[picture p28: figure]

Source model: “Anchorage Set” / Trolley v1.3.FCStd

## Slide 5

P0206 | Aluminum Profile L shape 30x30x1,5 with rail shape R
P0207 | Aluminum Profile L shape 30x30x1,5 with rail shape L
P0382 | 3mm washer


30x30x1,5 profile, 476mm long

140mm


3mm width

77mm


Source model: “Rail Set” / Trolley v1.3.FCStd

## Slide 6

P0322 | Anchorage front limit


18mm length

Source model: “Anchorage Set” / Trolley v1.3.FCStd

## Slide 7

P0011 | 135 degree bracket

Units: 4 + 4, Printer file: 135deg bracket type 002 x8.gcode (x8 parts)
Material: PLA, Color: Gray, Weight: 63g, Printing time: 4h 18m
Assembly: Chassis Top, Chassis Bottom
Source Model: “135 degree bracket type 002” / 135 degree bracket.FCStd


P0021 | 90 degree bracket

Units: 4 + 2, Printer file: 30x30 corner bracket type 002 x6.gcode (x6 parts)
Material: PLA, Color: Gray, Weight: 48g, Printing time: 3h 26m
Assembly: Chassis Middle, Set limit motors Top
Source Model: “30x30 corner bracket type 002” / AGV-Parts v4.FCStd


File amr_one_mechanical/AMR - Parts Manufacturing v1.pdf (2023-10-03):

# AMR

## Parts manufacturing

## P0015 135deg_small_braket M6 3holes

Units: 4 + 4
Assembly: Chassis Top, Chassis Bottom

Source model: “Aluminum 30mm x 3mm flat bar” / 135degree_small_braket v2.FCStd

Length: 210mm, diameter: 16mm, wall: 0,5mm Cut angle: 90deg both sides
Units: 1
Assembly: Clutch set
P0430 | Clutch axel (tube 410x16mm)
P0435 | Balancing axel (tube 390x16mm) | Length: 210mm, diameter: 16mm, wall: 0,5mm Cut angle: 90deg both sides Units: 1 Assembly: Balancing axel set


P0390 | Clutch lever (100x5mm bar) | Length: 100mm, diameter: 5mm Cut angle: 90deg both sides Units: 1 Assembly: Clutch set



P0160 | 30x30 204mm profile 22,5deg cut
P0165 | 30x30 138mm profile 22,5deg cut
P0155 | 30x30 339 mm profile flat cut | Units: 2 + 2 Assembly: Chassis Top, Chassis Bottom
P0170 | 30x30_200mm profile flat cut
P0175 | 30x30_60mm profile flat cut | Units: 4 Assembly: Chassis Middle
| | Units: 2 Assembly: Set limit motors Top

Length long side: 204mm
Cut angle: 22,5deg both sides
Units: 4 + 4
Assembly: Chassis Top, Chassis Bottom

Length long side: 138mm
Cut angle: 22,5deg both sides
Units: 4 + 4
Assembly: Chassis Top, Chassis Bottom

Source model for all: “30x30 profile” / 30x30 profiles.FCStd

NOTE: In the 4 units for “Chassis Bottom” make an 8,2mm hole in the middle for caster wheels

## P0185 Alu Profile L shape 15x15x1,5 106mm

Length long side: 206mm
Cut angle: 90deg
Units: 1+1
Assembly: Laser beam area – Bottom, Laser beam area – Top

Source Model: “Aluminum Profile L shape type 004” / Aluminum Profiles.FCStd


## P0190 Alu Profile L shape 15x15x1,5 135mm 22,5 deg

Length long side: 135mm
Cut angle: 22,5deg both sides
Units: 2 + 2
Assembly: Laser beam area – Bottom, Laser beam area – Top

## P0195 Alu Profile L shape 15x15x1,5 137,5mm 22,5deg

Length long side: 137,5mm
Cut angle: 22,5deg both sides
Units: 2 + 2
Assembly: Laser beam area – Bottom, Laser beam area – Top

Source Model for all: “Aluminum Profile L shape type 002” / Aluminum Profiles.FCStd

NOTE: Install M5
threaded rivet as
shown

## P0200 Alu Profile L shape 15x15x1,5 197mm

Length long side: 197mm
Cut angle: 90deg both sides Units: 2
Assembly: Laser beam area – Top

Source Model: “Aluminum Profile L shape type 003” / Aluminum Profiles.FCStd

## P0205 Aluminum Profile L shape 20x20x1,5 195mm 22,5 deg

Length long side: 195mm
Cut angle: 22,5deg both sides Units: 2
Assembly: Laser beam area – Bottom

Source Model: “Aluminum Profile L shape type 005” / Aluminum Profiles.FCStd

## P0215 Alu Profile square 10x10x1 259mm with holes


Length long side: 259mm
Cut angle: 90deg both sides Units: 2
Assembly: Chassis Middle

Source Model: “Z_Alu Profile square 10x10x1 with holes” / Aluminum Profiles.FCStd

NOTE: Install M5
threaded rivet as
shown


P0220 | Aluminum Profile L shape 30x20x1,5 250mm Length long side: 250mm Cut angle: 90deg both sides Units: 2 Assembly: Batteries support
P0230 | Aluminum Profile L shape 30x20x1,5 98mm Length long side: 98mm Cut angle: 90deg both sides Units: 2 Assembly: Batteries support

Source Model for all: “Aluminum Profile L shape type 001” / Aluminum Profiles.FCStd

## P0445 DIN Rail 260mm

Length: 260mm
Cut angle: 90deg both sides
Units: 1
Assembly: Flexisoft set

NOTE: AGV_Soporte_motor_D (30mm diameter) overlaps 7mm


P0325

P0325

P0340

P0350 | P0350
P0355

P0355

P0375 | P0375

P0380a

P0380b

P0380b

P0370 | P0370 | P0345 | P0345
P0360 | P0360 | P0365 | P0365

## P0325 Laser Support

Source: Plastic sheet 3mm
Units: 2
Assembly: Laser Set

Source Model: “Laser Supports” / Laser supports.FCStd

## P0340 PVC 3mm piece: Top cover


Source Model: “Top cover” / AGV-Parts v4.FCStd

Source: Plastic sheet 3mm, 405x405mm Color: Gray
Units: 1
Assembly: Top cover set

## P0345 PVC 3mm piece: Front Side-Bottom Cover


Source Model: “Front Side-Bottom Cover” / AGV-Parts v4.FCStd

Source: Plastic sheet 3mm
Color: White
Units: 2
Assembly: Sides cover Set

## P0370 PVC 3mm piece: Front Side-Top Cover


Source Model: “Front Side-Top Cover” / AGV-Parts v4.FCStd

Source: Plastic sheet 3mm
Color: White
Units: 2
Assembly: Sides cover Set

## P0360 PVC 3mm piece: Lateral-Top Cover


Source Model: “Lateral-Top Cover” / AGV-Parts v4.FCStd

Source: Plastic sheet 3mm
Color: White
Units: 2
Assembly: Sides cover Set

## P0365 PVC 3mm piece: Lateral-Bottom Cover


Source Model: “Lateral-Bottom Cover” / AGV-Parts v4.FCStd

Source: Plastic sheet 3mm
Color: White
Units: 2
Assembly: Sides cover Set


Source Model: “Lateral-Back Cover” / AGV-Parts v4.FCStd

Source: Plastic sheet 3mm
Color: Gray
Units: 2
Assembly: Sides cover Set

## P0350 PVC 3mm piece: Lateral-Back Cover

Source Model: “Back Side Cover” / AGV-Parts v4.FCStd

Source: Plastic sheet 3mm
Color: Gray
Units: 2
Assembly: Sides cover Set

## P0355 PVC 3mm piece: Back Side Cover

## P0375 PVC 3mm piece: laser beam area sheet

Source Model: “laser beam area sheet” / AGV-Parts v4.FCStd

Source: Plastic sheet 3mm, 261 x 405 mm
Color: Gray
Units: 1 + 1
Assembly: Laser beam area – Bottom / Laser beam area – Top

Cut all this part

## P0380 PVC 3mm piece: Inside wall (Part 1)


Source Model: “Inside wall” / AGV-Parts v4.FCStd

Source: Plastic sheet 3mm
Color: Gray
Units: 1
Assembly: Sides cover Set

NOTES:
Could be done in one long piece (530x60), or split in three: -Central part (from piece 103x60mm)
-2 Side parts (from 2 pieces 212x60mm)

## P0380 PVC 3mm piece: Inside wall (Part 2)


Source Model: “Inside wall” / AGV-Parts v4.FCStd

## P0410 Bracket front laser


Source Model: “Bracket front laser” / AGV-Parts v4.FCStd

Source: Aluminum sheet 30x1,5mm
Units: 2 + 2
Assembly: Laser beam area – Bottom / Laser beam area – Top

## P0415 Drive support


Source Model: “Drive support” / AGV-Parts v4.FCStd

Source: Aluminum sheet 20x118x1,5mm Units: 2
Assembly: Drives set

Install 2 M5 threaded rivets as shown in the picture. Each piece has the rivet in a different hole.

## P0425 Bracket RFID


Source Model: “Aluminum Profile L shape type 006” / Aluminum Profiles.FCStd

Source: Aluminum sheet 30x1,5mm Units: 2
Assembly: RFID Set
NOTE: Install M4 threaded rivet as shown (note it is in different hole in each piece)


Units: 1, Printer file: AGV_Soporte_motor_D_v1.gcode
Material: PLA, Color: Gray, Weight: 44g, Printing time: 2h 33m Assembly: Motors+Encoders
Source Model: “AGV_Soporte_motor_D” / AGV_Soporte_motor_D_v1.FCStd
P0290 | AGV_Soporte_motor_D
P0295 | AGV_Soporte_motor_I

Units: 1, Printer file: AGV_Soporte_motor_I_v4.gcode
Material: PLA, Color: Gray, Weight: 44g, Printing time: 2h 33m Assembly: Motors+Encoders
Source Model: “AGV_Soporte_motor_I” / AGV_Soporte_motor_I_v4.FCStd

## P0300 AGV_Rueda

Units: 2, Printer file: AGV_Rueda_v3.gcode
Material: PLA, Color: Gray, Weight: 44g, Printing time: 4h Assembly: Motors+Encoders
Source Model: “AGV_Rueda” / AGV_Rueda_v3.FCStd

## P0260 Axel clamp

Units: 1 + 1, Printer file: Axel clamp x2.gcode (2 units at once) Material: PLA, Color: Gray, Weight: 20g, Printing time: 1h 13m Assembly: Balancing axel set, Clutch set
Source Model: “Axel clamp” / Axel clamp.FCStd


Units: 1a & 1b, Printer file: 16mm axel corner clamp side a_b long.gcode (both in one) Material: PLA, Color: Gray, Weight: 21g, Printing time: 1h 24m
Assembly: Balancing axel set
Source Model: “16mm axel corner clamp side a long” / AGV_Clamp_eje_bal_v3.FCStd Source Model: “16mm axel corner clamp side b long” / AGV_Clamp_eje_bal_v3.FCStd
P0265 | Clutch-cam A
P0270 | Clutch-cam B
P0250 | 16mm axel corner clamp side a long
P0255 | 16mm axel corner clamp side b long

Units: 1A & 1B, Printer file: Clutch Cam A and B.gcode (both in one) Material: PLA, Color: Gray, Weight: 32g, Printing time: 1h 48m Assembly: Clutch set
Source Model: “Clutch-cam A” / Clutch Cam A and B.FCStd
Source Model: “Clutch-cam B” / Clutch Cam A and B.FCStd


Units: 1 & 1A & 1B, Printer file: Clutch axel clamps and cap.gcode (all in one) Material: PLA, Color: Gray, Weight: 14g, Printing time: 56m
Assembly: Clutch set
Source Model: “Clutch axel clamp A” / Clutch axel clamps.FCStd
Source Model: “Clutch axel clamp B” / Clutch axel clamps.FCStd Source Model: “Clutch axel cup” / Clutch axel cup.FCStd
P0275 | Clutch axel cap
P0280 | Clutch axel clamp A
P0285 | Clutch axel clamp B

Units: 4 + 4, Printer file: 135deg bracket type 002 x8.gcode (x8 parts) Material: PLA, Color: Gray, Weight: 63g, Printing time: 4h 18m Assembly: Chassis Top, Chassis Bottom
Source Model: “135 degree bracket type 002” / 135 degree bracket.FCStd


Units: 4 + 4, Printer file: 135deg_small_braket M6 3holes type 002 x8.gcode (x8 parts) Material: PLA, Color: Gray, Weight: 60g, Printing time: 4h 5m
Assembly: Chassis Top, Chassis Bottom
Source Model: “135deg_small_braket M6 3holes ” / 135degree_small_braket v2.FCStd

Units: 4 + 2, Printer file: 30x30 corner bracket type 002 x6.gcode (x6 parts) Material: PLA, Color: Gray, Weight: 48g, Printing time: 3h 26m Assembly: Chassis Middle, Set limit motors Top
Source Model: “30x30 corner bracket type 002” / AGV-Parts v4.FCStd
P0011 | 135 degree bracket
P0016 | 135deg_small_braket M6 3holes
P0021 | 90 degree bracket

Units: 2 + 2, Printer file: Bracket Front Laser type 002 x4.gcode (x4 parts) Material: PLA, Color: Gray, Weight: 11g, Printing time: 45m
Assembly: Laser beam area – Bottom / Laser beam area – Top
Source Model: “Bracket Front Laser type 002” / AGV-Parts v4.FCStd

## P0411 Bracket front laser

Units: 1, Printer file: Back top Cover v2.gcode
Material: PLA, Color: White, Weight: 107g, Printing time: 6h 33m Assembly: Back Cover Set
Source Model: “Back top Cover v2” / AGV-Parts v4.FCStd


Units: 1, Printer file: Back bottom Cover.gcode
Material: PLA, Color: White, Weight: 92g, Printing time: 5h 23m Assembly: Back Cover Set
Source Model: “Back bottom Cover” / AGV-Parts v4.FCStd


Units: 2, Printer file: RPiBox.gcode
Material: PLA, Color: White, Weight: 49g, Printing time: 3h 12m Assembly: Back Cover Set
Source Model: “RPiBox” / AGV-Parts v4.FCStd
P0315 | Back top Cover
P0320 | Back bottom Cover
P0316 | RPiBox

Units: 1, Printer file: Front Top Cover.gcode
Material: PLA, Color: White, Weight: 94g, Printing time: 5h Assembly: Front Cover Set
Source Model: “Front Top Cover” / AGV-Parts v4.FCStd

Units: 1, Printer file: Front Bottom Cover.gcode
Material: PLA, Color: White, Weight: 96g, Printing time: 4h 50m Assembly: Front Cover Set
Source Model: “Front Bottom Cover” / AGV-Parts v4.FCStd
P0305 | Front Top Cover
P0310 | Front Bottom Cover

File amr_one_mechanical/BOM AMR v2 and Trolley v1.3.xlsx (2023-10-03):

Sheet: BOM
BOM AGV
 |  |  |  |  |  |  |  |  |  |  |  |  |  |  |  |  | 1 | 1 | 1 | 2 | 5 | 3 | 3 | 3 | 3 | 4 | 4 | 4 | 4 | 2 | 2 |  | 5 | 4 | 2 | 2 | 6 | 2 | 6
 |  |  |  |  |  | Parts group |  |  |  |  |  |  |  |  |  |  | Assemblies
Ref. Code | Part | Item español | DIN | Name in CAD | File where design is | Brackets | Washers | Nuts | Screws | Profiles | 3D Printed Parts | Sheets | Other mechanical parts | Other | Price | Supplier Link | Chassis Top | Chassis Bottom | Chassis Middle | Batteries support | Flexisoft set | Set limit motors Top | Balancing axel set | Clutch set | Motors+Encoders | Laser Set | Laser beam area – Inside | Laser beam area – Bottom | Laser beam area – Top | PLC Set | Drives set | ACKSys Airlink set | Back Cover Set | Front Cover Set | Caster wheels set | Magnetic Sensor set | Top cover set | RFID Set | Sides cover Set |  | Notas
P0010 | 135 degree bracket |  |  | 135 degree bracket type 001 | 135 degree bracket | x |  |  |  |  |  |  |  |  |  | https://www.amazon.com/RUN-Aluminum-Profile-Brackets-Connectors/dp/B085VQZ66D?s=industrial | 0 | 0 |  |  |  |  |  |  |  |  |  |  |  |  |  |  |  |  |  |  |  |  |  | 0
P0011 | 135 degree bracket |  |  | 135 degree bracket type 002 | 135 degree bracket | x |  |  |  |  | x |  |  |  |  |  | 4 | 4 |  |  |  |  |  |  |  |  |  |  |  |  |  |  |  |  |  |  |  |  |  | 8
P0015 | 135deg_small_braket M6 3holes |  |  | 135deg_small_braket M6 3holes | 135degree_small_braket v2 | x |  |  |  |  |  | x |  |  |  |  | 0 | 0 |  |  |  |  |  |  |  |  |  |  |  |  |  |  |  |  |  |  |  |  |  | 0 | Made with 3cm aluminum flat bar
P0016 | 135deg_small_braket M6 3holes |  |  | 135deg_small_braket M6 3holes Type002 | 135degree_small_braket v2 | x |  |  |  |  | x |  |  |  |  |  | 4 | 4 |  |  |  |  |  |  |  |  |  |  |  |  |  |  |  |  |  |  |  |  |  | 8 | Made with 3cm aluminum flat bar
P0020 | 90 degree bracket |  |  | 3030 corner bracket.stp | AGV-Parts v4 | x |  |  |  |  |  |  |  |  | 1.00 € | https://www.amazon.com/Boeray-Bracket-Aluminum-Extrusion-Profile/dp/B01GJ34D2C?rnid=3071213011&s=industrial |  |  | 0 |  |  | 0 |  |  |  |  |  |  |  |  |  |  |  |  |  |  |  |  |  | 0
P0021 | 90 degree bracket |  |  | 30x30 corner bracket type 002 | AGV-Parts v4 | x |  |  |  |  | x |  |  |  | 1.00 € | https://www.amazon.com/Boeray-Bracket-Aluminum-Extrusion-Profile/dp/B01GJ34D2C?rnid=3071213011&s=industrial |  |  | 4 |  |  | 2 |  |  |  |  |  |  |  |  |  |  |  |  |  |  |  |  |  | 6
P0022 | 90 degree bracket (small) |  |  |  |  | x |  |  |  |  |  |  |  |  | 1.00 € | https://www.amazon.com/PZRT-Aluminum-Fastener-Standard-Extrusion/dp/B07H89R3QR
P0025 | 90 degree bracket |  |  |  |  | x |  |  |  |  |  |  |  |  |  | https://www.amazon.com/80-20-2-Hole-Inside-Bracket/dp/B001IA2LYE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 |  |  |  |  |  |  |  |  |  |  |  |  |  |  |  |  |  |  |  |  |  |  |  | 0
P0030 | 45 degree bracket |  |  |  |  | x |  |  |  |  |  |  |  |  |  | https://www.amazon.com/uxcell-Aluminum-Brackets-Profile-Connectors/dp/B07SHH11CK?s=industrial |  |  |  |  |  |  |  |  |  |  |  |  |  |  |  |  |  |  |  |  |  |  |  | 0
P0035 | Washer M6 | Arandela M6 |  | Washer M6 |  |  | x |  |  |  |  |  |  |  |  | https://www.amazon.es/gp/product/B073GQLNL2 | 8 | 8 | 12 |  | 1 | 4 | 6 | 10 | 0 | 8 | 4 |  |  |  | 2 |  |  |  |  |  |  | 2 |  | 65
P0040 | Washer M5 |  |  | Washer M5 |  |  | x |  |  |  |  |  |  |  |  |  |  |  |  |  |  |  |  |  | 2 | 4 | 0 |  |  | 6 | 4 |  |  |  |  |  |  |  |  | 16
P0045 | Washer M8 |  |  | Washer M8 |  |  | x |  |  |  |  |  |  |  |  |  |  |  |  |  |  |  |  |  |  |  |  |  |  |  |  |  |  |  | 16 |  |  |  |  | 16
P0050 | T Nut M6 3030 | Tuerca en T para perfil 3030 M6 |  | T-slot nut M6 3030 |  |  |  | x |  |  |  |  |  |  |  | https://www.amazon.es/gp/product/B075WWWTYB/ref=crt_ewc_title_srh_5?ie=UTF8&psc=1&smid=A5QX2SUPA7LK7 | 20 | 20 | 12 | 8 | 1 | 4 | 6 | 8 |  | 4 | 4 | 0 | 0 | 0 | 2 | 0 | 0 | 0 | 0 | 0 | 0 | 2 | 0 | 91
P0055 | T Nut M5 3030 | Tuerca en T para perfil 3030 M6 |  |  |  |  |  | x |  |  |  |  |  |  |  | https://www.amazon.es/gp/product/B075WV9GRD/ref=crt_ewc_img_dp_6?ie=UTF8&psc=1&smid=A5QX2SUPA7LK7 | 0 | 0 | 0 | 0 | 0 | 0 | 0 | 0 |  |  |  | 0 | 0 | 3 | 4 | 2 | 4 | 4 | 0 | 0 | 8 | 0 | 48 | 73
P0060 | ISO4032_Hex_Nut_M6 |  |  |  |  |  |  | x |  |  |  |  |  |  |  |  |  |  |  |  |  |  |  | 2 |  |  |  |  |  |  |  |  |  |  |  |  |  |  |  | 2
P0065 | ISO4032_Hex_Nut_M8 |  |  | HEX Nut M8 |  |  |  | x |  |  |  |  |  |  |  |  |  |  |  |  |  |  |  |  |  |  |  |  |  |  |  |  |  |  | 4 |  |  |  |  | 4
P0070 | 30x30 inner corner L nut |  |  |  |  |  |  | x |  |  |  |  |  |  |  | https://www.amazon.com/uxcell-Interior-Connector-Aluminum-Extrusion/dp/B07VP59DY5 |  |  | 4 |  |  |  |  |  |  |  |  |  |  |  |  |  |  |  |  |  |  |  |  | 4
P0075 | Screws for inner corner L nut |  |  |  |  |  |  | x |  |  |  |  |  |  |  | https://www.amazon.es/Inoxidable-Tornillo-Prisionero-Hexagonal-Surtido/dp/B07PKMC57C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 |  |  | 8 |  |  |  |  |  |  |  |  |  |  |  |  |  |  |  |  |  |  |  |  | 8
P0080 | Countersunk flat head Cap Screws M6 x 14 | Tornillo M6x14 cabeza plana avellanada allen | DIN7991 | Screw_M6x14_CS |  |  |  |  | x |  |  |  |  |  |  | https://www.amazon.es/Tornillo-avellanado-hexagonal-m%C3%A1quina-perno/dp/B07XF1CG8X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 | 0 | 0 |  | 8 |  |  |  |  | 6 |  |  |  |  |  |  |  |  |  |  |  |  |  |  | 14 | Para perfiles 135 grados
 | Countersunk flat head Cap Screws M6 x 12 | Tornillo M6x14 cabeza plana avellanada allen | DIN7991 | Screw_M6x12_CS |  |  |  |  | x |  |  |  |  |  |  |  |  |  |  |  |  |  |  |  |  |  |  |  |  |  |  |  |  |  |  |  |  |  |  | 0
 | Countersunk flat head Cap Screws M5 x 12 |  |  | Screw_M5x12_CS |  |  |  |  | x |  |  |  |  |  |  | https://www.amazon.es/dp/B07Y5D5MZK (https://www.amazon.es/dp/B07Y5D5MZK?spLa=ZW5jcnlwdGVkUXVhbGlmaWVyPU) |  |  |  |  |  |  |  |  |  |  | 4 |  |  |  |  |  |  |  |  |  | 8 |  | 48 | 60
 | Countersunk flat head Cap Screws M3 x 12 |  |  | Screw_M3x12_CS |  |  |  |  | x |  |  |  |  |  |  | https://www.amazon.es/S2FIX-M3-SCS-PARENT-Llave-de-vaso-hexagonal/dp/B07MCH9QSH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 |  |  |  |  |  |  |  |  |  |  |  |  |  |  |  |  | 4 |  |  |  |  |  |  | 4
P0090 | Screw_M4x12 HEX |  |  | Screw_M4x12_ISO4762 |  |  |  |  | x |  |  |  |  |  |  |  |  |  |  |  |  |  |  |  |  |  |  |  |  |  |  |  |  |  |  |  |  | 2 |  | 2
P0095 | Screw_M5x12 HEX |  |  | Screw_M5x12_ISO4762 |  |  |  |  | x |  |  |  |  |  |  |  |  |  |  |  |  |  |  |  |  | 4 |  |  |  |  |  | 2 | 4 | 4 |  |  |  |  |  | 14
P0100 | Screw_M5x14 HEX |  |  | Screw_M5x14_ISO4762 |  |  |  |  | x |  |  |  |  |  |  |  |  |  |  |  |  |  |  |  |  |  | 0 |  |  |  |  |  |  |  |  |  |  |  |  | 0
P0105 | Screw_M5x16 HEX |  |  | Screw_M5x16_ISO4762 |  |  |  |  | x |  |  |  |  |  |  |  |  |  |  |  |  |  |  |  | 2 |  |  |  |  |  |  |  |  |  |  |  |  |  |  | 2
P0110 | Screw_M5x25 HEX |  |  | Screw_M5x25_ISO4762 |  |  |  |  | x |  |  |  |  |  |  |  |  |  |  |  |  |  |  |  |  |  |  |  |  | 0 |  |  |  |  |  |  |  |  |  | 0
P0115 | Screw_M5x30 HEX |  |  | Screw_M5x30_ISO4762 |  |  |  |  | x |  |  |  |  |  |  | https://www.amazon.es/Tornillo-cil%C3%ADndrico-inoxidable-longitudes-Multicolor/dp/B082FQXXD8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 (https://www.amazon.es/Tornillo-cilíndrico-inoxidable-longitudes-Multicolor/dp/B082FQXXD8?__mk_es_ES=ÅMÅŽÕÑ&rnid=1703620031&s=tools) |  |  |  |  |  |  |  |  |  |  |  |  |  | 3 | 4 |  |  |  |  |  |  |  |  | 7
P0120 | Screw_M6x12 HEX | Tornillo M6x16 hex |  | Screw_M6x12_ISO4762 |  |  |  |  | x |  |  |  |  |  |  |  |  |  |  |  |  |  |  |  |  |  |  |  |  |  |  |  |  |  |  |  |  | 0 |  | 0
P0125 | Screw_M6x14 HEX | Tornillo M6x16 hex |  | Screw_M6x14_ISO4762 |  |  |  |  | x |  |  |  |  |  |  | https://www.amazon.es/Xiedeai-Carbono-Hexagonales-Tornillo-Cabeza/dp/B07RMXVH98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 | 20 | 20 | 8 |  | 1 | 4 | 6 | 6 | 0 | 4 | 4 |  |  |  | 2 |  |  |  |  |  |  | 2 |  | 77
P0130 | Screw_M6x16 HEX | Tornillo M6x16 hex |  | Screw_M6x16_ISO4762 |  |  |  |  | x |  |  |  |  |  |  |  | 0 | 0 | 0 |  | 0 | 0 | 0 | 0 | 0 | 0 |  |  |  |  |  |  |  |  |  |  |  |  |  | 0
P0135 | Screw_M6x20 HEX |  |  | Screw_M6x20_ISO4762 |  |  |  |  | x |  |  |  |  |  |  | https://www.amazon.es/Tornillos-Sujetadores-Reborde-Inoxidable-Hexagonal/dp/B0746CFPZ8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 |  |  | 4 |  |  |  |  |  |  |  |  |  |  |  |  |  |  |  |  |  |  |  |  | 4
P0140 | Screw_M6x35 HEX |  |  | Screw_M6x35_ISO4762 |  |  |  |  | x |  |  |  |  |  |  | https://www.amazon.es/hexagonal-Socket-Pernos-tornillo-20-unidades/dp/B084RMFYZG |  |  |  |  |  |  |  | 2 |  |  |  |  |  |  |  |  |  |  |  |  |  |  |  | 2
 | M3x5 button hex screw |  |  | M3x5 BHCS |  |  |  |  | x |  |  |  |  |  |  |  |  |  |  |  |  |  |  |  |  |  |  |  |  |  |  |  | 4 |  |  |  |  |  |  | 4
P0145 | M5x12 button hex screw |  |  | M5x12 BHCS |  |  |  |  | x |  |  |  |  |  |  |  |  |  |  |  |  |  |  |  |  |  |  |  |  |  |  |  | 0 | 0 |  | 2 | 0 |  |  | 2 | Make threaded holes in aluminum beam FOR MAG SENSOR
P0150 | Screw_M8x50 HEX HEAD |  |  | Bolt HEX M8x50 |  |  |  |  | x |  |  |  |  |  |  | https://www.amazon.es/Tornillos-de-cabeza-hexagonal-ISO-4017-M8x50-con-hex%C3%A1gono-externo-8-8-galvanizado-con-tuercas-ISO/dp/B086T124L8 |  |  |  |  |  |  |  |  |  |  |  |  |  |  |  |  |  |  | 4 |  |  |  |  | 4
P0155 | 30x30 339 mm profile flat cut | Perfil 30x30 339mm corte plano |  | 30x30_339mm profile | 30x30 profiles |  |  |  |  | x |  |  |  |  |  |  | 2 | 2 |  |  |  |  |  |  |  |  |  |  |  |  |  |  |  |  |  |  |  |  |  | 4
P0160 | 30x30 204mm profile 22,5deg cut | Perfil 30x30 204mm corte biselado 22,5º |  | 30x30_204mm_22.5deg profile | 30x30 profiles |  |  |  |  | x |  |  |  |  |  |  | 4 | 4 |  |  |  |  |  |  |  |  |  |  |  |  |  |  |  |  |  |  |  |  |  | 8
P0165 | 30x30 138mm profile 22,5deg cut | Perfil 30x30 138mm corte biselado 22,5º |  | 30x30_138mm_22.5deg profile | 30x30 profiles |  |  |  |  | x |  |  |  |  |  |  | 4 | 4 |  |  |  |  |  |  |  |  |  |  |  |  |  |  |  |  |  |  |  |  |  | 8
P0170 | 30x30_200mm profile flat cut |  |  | 30x30_200mm profile | 30x30 profiles |  |  |  |  | x |  |  |  |  |  |  |  |  | 4 |  |  |  |  |  |  |  |  |  |  |  |  |  |  |  |  |  |  |  |  | 4
P0175 | 30x30_60mm profile flat cut |  |  | 30x30_60mm profile | 30x30 profiles |  |  |  |  | x |  |  |  |  |  |  |  |  |  |  |  | 2 |  |  |  |  |  |  |  |  |  |  |  |  |  |  |  |  |  | 2
P0185 | Alu Profile L shape 15x15x1,5 106mm |  |  | Alu Profile L shape 15x15x1,5 106mm front_laser | Aluminum Profiles |  |  |  |  | x |  |  |  |  |  | https://www.leroymerlin.es/fp/10209941/perfil-forma-en-l-de-aluminio-lacado-lacado |  |  |  |  |  |  |  |  |  |  | 0 | 1 | 1 |  |  |  |  |  |  |  |  |  |  | 2
P0190 | Alu Profile L shape 15x15x1,5 135mm 22,5deg |  |  | Alu Profile L shape 15x15x1,5 135mm 22,5deg t-rivets | Aluminum Profiles |  |  |  |  | x |  |  |  |  |  | https://www.leroymerlin.es/fp/10209941/perfil-forma-en-l-de-aluminio-lacado-lacado |  |  |  |  |  |  |  |  |  |  |  | 2 | 2 |  |  |  |  |  |  |  |  |  |  | 4
P0195 | Alu Profile L shape 15x15x1,5 137,5mm 22,5deg |  |  | Alu Profile L shape 15x15x1,5 137,5mm 22,5deg t-rivets | Aluminum Profiles |  |  |  |  | x |  |  |  |  |  | https://www.leroymerlin.es/fp/10209941/perfil-forma-en-l-de-aluminio-lacado-lacado |  |  |  |  |  |  |  |  |  |  |  | 2 | 2 |  |  |  |  |  |  |  |  |  |  | 4
P0200 | Alu Profile L shape 15x15x1,5 197mm |  |  | Alu Profile L shape 15x15x1,5 197mm | Aluminum Profiles |  |  |  |  | x |  |  |  |  |  | https://www.leroymerlin.es/fp/10209941/perfil-forma-en-l-de-aluminio-lacado-lacado |  |  |  |  |  |  |  |  |  |  | 0 |  | 2 |  |  |  |  |  |  |  |  |  |  | 2
P0205 | Aluminum Profile L shape 20x20x1,5 195mm 22,5deg |  |  | Alu Profile L shape type005 20x20x1,5 195mm | Aluminum Profiles |  |  |  |  | x |  |  |  |  |  | https://www.leroymerlin.es/fp/529074/perfil-forma-en-l-de-aluminio-anodizado-anodizado |  |  |  |  |  |  |  |  |  |  | 0 | 2 |  |  |  |  |  |  |  |  |  |  |  | 2
P0215 | Alu Profile square 10x10x1 259mm with holes |  |  | Alu Profile square 10x10x1 259mm with holes | Aluminum Profiles |  |  |  |  | x |  |  |  |  |  | https://www.leroymerlin.es/fp/707770/perfil-forma-tubo-cuadrado-de-aluminio-en-bruto-en-bruto |  |  | 2 |  |  |  |  |  |  |  |  |  |  |  |  |  |  |  |  |  |  |  |  | 2
P0220 | Aluminum Profile L shape 30x20x1,5 250mm |  |  | Aluminum Profile L shape type 001 30x20x1,5 250mm | Aluminum Profiles |  |  |  |  | x |  |  |  |  |  | https://www.leroymerlin.es/fp/11434360/perfil-forma-en-l-de-aluminio-anodizado-anodizado |  |  |  | 2 |  |  |  |  |  |  |  |  |  |  |  |  |  |  |  |  |  |  |  | 2
P0225 | Aluminum Profile L shape 30x20x1,5 108mm |  |  | Aluminum Profile L shape type 001 30x20x1,5 108mm | Aluminum Profiles |  |  |  |  | x |  |  |  |  |  | https://www.leroymerlin.es/fp/11434360/perfil-forma-en-l-de-aluminio-anodizado-anodizado |  |  |  | 0 |  |  |  |  |  |  |  |  |  |  |  |  |  |  |  |  |  |  |  | 0
P0230 | Aluminum Profile L shape 30x20x1,5 98mm |  |  | Aluminum Profile L shape type 001 30x20x1,5 98mm | Aluminum Profiles |  |  |  |  | x |  |  |  |  |  | https://www.leroymerlin.es/fp/11434360/perfil-forma-en-l-de-aluminio-anodizado-anodizado |  |  |  | 2 |  |  |  |  |  |  |  |  |  |  |  |  |  |  |  |  |  |  |  | 2
P0250 | 16mm axel corner clamp side a long |  |  | 16mm axel corner clamp side a long | AGV_Clamp_eje_bal_v3 |  |  |  |  |  | x |  |  |  |  |  |  |  |  |  |  |  | 1 |  |  |  |  |  |  |  |  |  |  |  |  |  |  |  |  | 1 | 3d printing part
P0255 | 16mm axel corner clamp side b long |  |  | 16mm axel corner clamp side b long | AGV_Clamp_eje_bal_v3 |  |  |  |  |  | x |  |  |  |  |  |  |  |  |  |  |  | 1 |  |  |  |  |  |  |  |  |  |  |  |  |  |  |  |  | 1 | 3d printing part
P0260 | Axel clamp |  |  | Axel clamp | Axel clamp |  |  |  |  |  | x |  |  |  |  |  |  |  |  |  |  |  | 1 | 1 |  |  |  |  |  |  |  |  |  |  |  |  |  |  |  | 2 | 3d printing part
P0265 | Clutch-cam A |  |  | Clutch-cam A | Clutch Cam A and B |  |  |  |  |  | x |  |  |  |  |  |  |  |  |  |  |  |  | 1 |  |  |  |  |  |  |  |  |  |  |  |  |  |  |  | 1 | 3d printing part
P0270 | Clutch-cam B |  |  | Clutch-cam B | Clutch Cam A and B |  |  |  |  |  | x |  |  |  |  |  |  |  |  |  |  |  |  | 1 |  |  |  |  |  |  |  |  |  |  |  |  |  |  |  | 1 | 3d printing part
P0275 | Clutch axel cap |  |  | Clutch axel cup | Clutch axel cup |  |  |  |  |  | x |  |  |  |  |  |  |  |  |  |  |  |  | 1 |  |  |  |  |  |  |  |  |  |  |  |  |  |  |  | 1 | 3d printing part
P0280 | Clutch axel clamp A |  |  | Clutch axel clamp A | Clutch axel clamps |  |  |  |  |  | x |  |  |  |  |  |  |  |  |  |  |  |  | 1 |  |  |  |  |  |  |  |  |  |  |  |  |  |  |  | 1 | 3d printing part
P0285 | Clutch axel clamp B |  |  | Clutch axel clamp B | Clutch axel clamps |  |  |  |  |  | x |  |  |  |  |  |  |  |  |  |  |  |  | 1 |  |  |  |  |  |  |  |  |  |  |  |  |  |  |  | 1 | 3d printing part
P0290 | AGV_Soporte_motor_D |  |  | AGV_Soporte_motor_D | AGV_Soporte_motor_D_v1 |  |  |  |  |  | x |  |  |  |  |  |  |  |  |  |  |  |  |  | 1 |  |  |  |  |  |  |  |  |  |  |  |  |  |  | 1 | 3d printing part
P0295 | AGV_Soporte_motor_I |  |  | AGV_Soporte_motor_I | AGV_Soporte_motor_I_v4 |  |  |  |  |  | x |  |  |  |  |  |  |  |  |  |  |  |  |  | 1 |  |  |  |  |  |  |  |  |  |  |  |  |  |  | 1 | 3d printing part
P0300 | AGV_Rueda |  |  | AGV_Rueda | AGV_Rueda_v3 |  |  |  |  |  | x |  |  |  |  |  |  |  |  |  |  |  |  |  | 2 |  |  |  |  |  |  |  |  |  |  |  |  |  |  | 2 | 3d printing part
P0305 | Front Top Cover |  |  | Front Top Cover | AGV-Parts v4 |  |  |  |  |  | x |  |  |  |  |  |  |  |  |  |  |  |  |  |  |  |  |  |  |  |  |  |  | 1 |  |  |  |  |  | 1 | 3d printing part
P0310 | Front Bottom Cover |  |  | Front Bottom Cover | AGV-Parts v4 |  |  |  |  |  | x |  |  |  |  |  |  |  |  |  |  |  |  |  |  |  |  |  |  |  |  |  |  | 1 |  |  |  |  |  | 1 | 3d printing part
P0315 | Back top Cover |  |  | Back top Cover v2 | AGV-Parts v4 |  |  |  |  |  | x |  |  |  |  |  |  |  |  |  |  |  |  |  |  |  |  |  |  |  |  |  | 1 |  |  |  |  |  |  | 1 | Back top Cover v2.gcode /100gr, 9h
P0316 | RPiBox |  |  | RPiBox | AGV-Parts v4 |  |  |  |  |  | x |  |  |  |  |  |  |  |  |  |  |  |  |  |  |  |  |  |  |  |  |  | 1 |  |  |  |  |  |  | 1 | RPiBox.gcode / 50gr, 3,5h
P0320 | Back bottom Cover |  |  | Back bottom Cover | AGV-Parts v4 |  |  |  |  |  | x |  |  |  |  |  |  |  |  |  |  |  |  |  |  |  |  |  |  |  |  |  | 1 |  |  |  |  |  |  | 1 | Back bottom Cover.gcode
P0325 | Laser Support |  |  | Laser Support | Laser supports |  |  |  |  |  |  | x |  |  |  |  |  |  |  |  |  |  |  |  |  | 2 |  |  |  |  |  |  |  |  |  |  |  |  |  | 2 | aluminum sheet piece
P0330 | Compact PVC sheet 3mm white 500x500 |  |  |  |  |  |  |  |  |  |  | x |  |  |  | https://www.mwmaterialsworld.com/es/plancha-pvc-rigido-satinado-blanco.html#formatos-header |  |  |  |  |  |  |  |  |  |  |  |  |  |  |  |  |  |  |  |  |  |  |  | 0
P0335 | PVC Espumado Blanco (forex) |  |  |  |  |  |  |  |  |  |  | x |  |  |  | https://www.mwmaterialsworld.com/es/plancha-pvc-espumado-blanco-forex.html |  |  |  |  |  |  |  |  |  |  |  |  |  |  |  |  |  |  |  |  |  |  |  | 0
P0340 | PVC 3mm piece: Top cover |  |  | Top cover | AGV-Parts v4 |  |  |  |  |  |  | x |  |  |  |  |  |  |  |  |  |  |  |  |  |  |  |  |  |  |  |  |  |  |  |  | 1 |  |  | 1 | Source: Plastic sheet 3mm, 405x405mm
P0345 | PVC 3mm piece: Front Side-Bottom Cover |  |  | Front Side-Bottom Cover | AGV-Parts v4 |  |  |  |  |  |  | x |  |  |  |  |  |  |  |  |  |  |  |  |  |  |  |  |  |  |  |  |  |  |  |  |  |  | 2 | 2 | Cut of PVC sheet
P0350 | PVC 3mm piece: Lateral-Back Cover |  |  | Lateral-Back Cover | AGV-Parts v4 |  |  |  |  |  |  | x |  |  |  |  |  |  |  |  |  |  |  |  |  |  |  |  |  |  |  |  |  |  |  |  |  |  | 2 | 2 | Cut of PVC sheet
P0355 | PVC 3mm piece: Back Side Cover |  |  | Back Side Cover | AGV-Parts v4 |  |  |  |  |  |  | x |  |  |  |  |  |  |  |  |  |  |  |  |  |  |  |  |  |  |  |  |  |  |  |  |  |  | 2 | 2 | Cut of PVC sheet
P0360 | PVC 3mm piece: Lateral-Top Cover |  |  | Lateral-Top Cover | AGV-Parts v4 |  |  |  |  |  |  | x |  |  |  |  |  |  |  |  |  |  |  |  |  |  |  |  |  |  |  |  |  |  |  |  |  |  | 2 | 2 | Cut of PVC sheet
P0365 | PVC 3mm piece: Lateral-Bottom Cover |  |  | Lateral-Bottom Cover | AGV-Parts v4 |  |  |  |  |  |  | x |  |  |  |  |  |  |  |  |  |  |  |  |  |  |  |  |  |  |  |  |  |  |  |  |  |  | 2 | 2 | Cut of PVC sheet
P0370 | PVC 3mm piece: Front Side-Top Cover |  |  | Front Side-Top Cover | AGV-Parts v4 |  |  |  |  |  |  | x |  |  |  |  |  |  |  |  |  |  |  |  |  |  |  |  |  |  |  |  |  |  |  |  |  |  | 2 | 2 | Cut of PVC sheet
P0375 | PVC 3mm piece: laser beam area sheet |  |  | laser beam area sheet | AGV-Parts v4 |  |  |  |  |  |  | x |  |  |  |  |  |  |  |  |  |  |  |  |  |  |  | 1 | 1 |  |  |  |  |  |  |  |  |  |  | 2 | Cut of PVC sheet
P0380 | PVC 3mm piece: Inside wall |  |  | Inside wall | AGV-Parts v4 |  |  |  |  |  |  | x |  |  |  |  |  |  |  |  |  |  |  |  |  |  | 1 |  |  |  |  |  |  |  |  |  |  |  |  | 1 | Cut of PVC sheet
P0385 | Rubber band 22mm wide |  |  |  |  |  |  |  |  |  |  |  | x |  |  |  |  |  |  |  |  |  |  |  | 2 |  |  |  |  |  |  |  |  |  |  |  |  |  |  | 2
P0390 | Clutch lever (100x5mm bar) |  |  |  |  |  |  |  |  |  |  |  | x |  |  |  |  |  |  |  |  |  |  | 1 |  |  |  |  |  |  |  |  |  |  |  |  |  |  |  | 1
P0395 | Threaded rivets M5 |  |  | M5 Threaded rivet |  |  |  |  |  |  |  |  | x |  |  |  |  |  | 4 |  |  |  |  |  |  |  |  | 8 | 8 |  | 2 |  |  |  |  |  |  |  |  | 22
P0400 | Threaded rivets M4 |  |  | M4 Threaded rivet |  |  |  |  |  |  |  |  | x |  |  |  |  |  |  |  |  |  |  |  |  |  |  |  |  |  |  |  |  |  |  |  |  | 2 |  | 2
P0405 | Rivet aluminum 4,2mm |  |  | 4,2mm_Rivet |  |  |  |  |  |  |  |  | x |  |  |  |  |  |  |  |  |  |  |  |  |  | 12 | 18 | 18 |  |  |  |  |  |  |  |  |  |  | 48
P0410 | Bracket front laser |  |  | Bracket front laser | AGV-Parts v4 |  |  |  |  |  |  |  | x |  |  |  |  |  |  |  |  |  |  |  |  |  |  | 0 | 0 |  |  |  |  |  |  |  |  |  |  | 0 | Made from aluminum flat bar 3cm
P0411 | Bracket front laser |  |  | Bracket Front Laser type 002 | AGV-Parts v4 |  |  |  |  |  | x |  | x |  |  |  |  |  |  |  |  |  |  |  |  |  |  | 2 | 2 |  |  |  |  |  |  |  |  |  |  | 4 | Made from aluminum flat bar 3cm
P0415 | Drive support |  |  | Drive support |  |  |  |  |  |  |  |  | x |  |  |  |  |  |  |  |  |  |  |  |  |  |  |  |  |  | 2 |  |  |  |  |  |  |  |  | 2 | Made from aluminum flat bar 2-3cm
P0420 | Caster wheels ALEX SERIE B-BP 3-0006 |  |  | Caster wheels ALEX SERIE B-BP 3-0006 | Imported |  |  |  |  |  |  |  | x |  | 3.50 € | http://www.gonzalezparadelo.com/patas-y-ruedas/562-rueda-serie-b-bp.html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 |  |  |  |  |  |  |  |  |  |  |  |  |  |  |  |  |  |  | 4 |  |  |  |  | 4 | Alex: https://www.alex.es/productos/0-ruedas-para-muebles-auxiliares/0-serie-b-bp/2388 https://www.carrefour.es/rueda-d-alex-b3-0006-40-mm/8422202300061/p
P0425 | Bracket RFID |  |  | Bracket 3x3 RFID | Aluminum Profiles |  |  |  |  |  |  |  | x |  |  |  |  |  |  |  |  |  |  |  |  |  |  |  |  |  |  |  |  |  |  |  |  | 2 |  | 2 | Made from aluminum flat bar 3cm
P0430 | Clutch axel (tube 410x16mm) |  |  |  |  |  |  |  |  |  |  |  | x |  |  |  |  |  |  |  |  |  |  | 1 |  |  |  |  |  |  |  |  |  |  |  |  |  |  |  | 1
P0435 | Balancing axel (tube 390x16mm) |  |  |  |  |  |  |  |  |  |  |  | x |  |  |  |  |  |  |  |  |  | 1 |  |  |  |  |  |  |  |  |  |  |  |  |  |  |  |  | 1
P0440 | Tope de agujas AXK1730-ZEN - 17x30x2 mm | Tope de agujas AXK1730-ZEN - 17x30x2 mm |  |  |  |  |  |  |  |  |  |  | x |  |  | https://www.123rodamiento.es/rodamiento-AXK1730-ZEN.php |  |  |  |  |  |  |  |  |  |  |  |  |  |  |  |  |  |  |  |  |  |  |  | 0 | For axels
P0445 | DIN Rail 260mm |  |  |  |  |  |  |  |  |  |  |  | x |  |  |  |  |  |  |  | 1 |  |  |  |  |  |  |  |  |  |  |  |  |  |  |  |  |  |  | 1
P0446 | Spring |  |  | Motor Spring | AGV-Parts v4 |  |  |  |  |  |  |  | x |  |  |  |  |  |  |  |  | 2 |  |  |  |  |  |  |  |  |  |  |  |  |  |  |  |  |  | 2
P0450 | Flexisoft modules |  |  |  | Imported |  |  |  |  |  |  |  |  | x |  |  |  |  |  |  | 1 |  |  |  |  |  |  |  |  |  |  |  |  |  |  |  |  |  |  | 1
P0455 | Motor_Nidec_404_385_ right side |  |  |  |  |  |  |  |  |  |  |  |  | x |  |  |  |  |  |  |  |  |  |  | 1 |  |  |  |  |  |  |  |  |  |  |  |  |  |  | 1
P0460 | Motor_Nidec_404_385_left side |  |  |  |  |  |  |  |  |  |  |  |  | x |  |  |  |  |  |  |  |  |  |  | 1 |  |  |  |  |  |  |  |  |  |  |  |  |  |  | 1
P0465 | Sick s300 safety laser |  |  |  | Imported |  |  |  |  |  |  |  |  | x |  |  |  |  |  |  |  |  |  |  |  | 1 |  |  |  |  |  |  |  |  |  |  |  |  |  | 1 | Also s300 mini
P0470 | Encoder |  |  |  |  |  |  |  |  |  |  |  |  | x |  |  |  |  |  |  |  |  |  |  | 2 |  |  |  |  |  |  |  |  |  |  |  |  |  |  | 2 | Encoders should be assembled…
P0475 | PLC IFM CR0303 |  |  | PLC IFM cr0303 | Imported |  |  |  |  |  |  |  |  | x |  |  |  |  |  |  |  |  |  |  |  |  |  |  |  | 1 |  |  |  |  |  |  |  |  |  | 1
P0480 | ACKSys |  |  |  |  |  |  |  |  |  |  |  |  | x |  |  |  |  |  |  |  |  |  |  |  |  |  |  |  |  |  | 1 |  |  |  |  |  |  |  | 1
P0485 | Antenna |  |  |  |  |  |  |  |  |  |  |  |  | x |  |  |  |  |  |  |  |  |  |  |  |  |  |  |  |  |  | 2 |  |  |  |  |  |  |  | 2
P0490 | Emergency stop button 19mm |  |  |  |  |  |  |  |  |  |  |  |  | x | 12.00 € | https://www.amazon.es/gp/product/B003UR5P8C/ref=ppx_yo_dt_b_asin_title_o02_s00?ie=UTF8&psc=1 |  |  |  |  |  |  |  |  |  |  |  |  |  |  |  |  | 1 |  |  |  |  |  |  | 1 | Más barato en aliexpress
P0495 | Momentary push button with white ring led 19mm |  |  |  |  |  |  |  |  |  |  |  |  | x | 11.00 € | https://www.amazon.es/dp/B07257ZHWR/?coliid=I1OZDEQCPLQ2F3&colid=21KFXZ928R9B2 |  |  |  |  |  |  |  |  |  |  |  |  |  |  |  |  | 1 |  |  |  |  |  |  | 1
P0500 | Battery capacity display |  |  |  |  |  |  |  |  |  |  |  |  | x | 10.00 € | https://www.amazon.es/gp/product/B07MM4RMTZ/ref=ppx_yo_dt_b_asin_title_o00_s00?ie=UTF8&psc=1 |  |  |  |  |  |  |  |  |  |  |  |  |  |  |  |  | 1 |  |  |  |  |  |  | 1
P0505 | Raspberry Pi 3B |  |  |  |  |  |  |  |  |  |  |  |  | x |  |  |  |  |  |  |  |  |  |  |  |  |  |  |  |  |  |  | 1 |  |  |  |  |  |  | 1
P0510 | 7 inch touch screen |  |  |  |  |  |  |  |  |  |  |  |  | x |  |  |  |  |  |  |  |  |  |  |  |  |  |  |  |  |  |  | 1 |  |  |  |  |  |  | 1
P0515 | Magnetic_Sensor_Macome_GS-4484 |  |  |  |  |  |  |  |  |  |  |  |  | x |  |  |  |  |  |  |  |  |  |  |  |  |  |  |  |  |  |  |  |  |  | 1 |  |  |  | 1
P0520 | Battery lead acid 12v, 12Ah DSK 10325 |  |  |  |  |  |  |  |  |  |  |  |  | x | 29.00 € | https://www.amazon.es/dp/B01N2HLZKQ/?coliid=IA7YSBL7MHHSJ&colid=21KFXZ928R9B2 |  |  |  |  |  |  |  |  |  |  |  |  |  |  |  |  |  |  |  |  |  |  |  | 0
P0525 | Battery charger 24v |  |  |  |  |  |  |  |  |  |  |  |  | x | 32.00 € | https://www.amazon.es/dp/B07XFLR2MR/?coliid=IIGKE8FGIL96X&colid=21KFXZ928R9B2 |  |  |  |  |  |  |  |  |  |  |  |  |  |  |  |  |  |  |  |  |  |  |  | 0
P0530 | Power switch 16A |  |  |  |  |  |  |  |  |  |  |  |  | x | 6.00 € | https://www.amazon.es/dp/B073PCDBP1/?coliid=I1W3HKWDY90KM&colid=21KFXZ928R9B2 |  |  |  |  |  |  |  |  |  |  |  |  |  |  |  |  |  |  |  |  |  |  |  | 0
P0535 | PG Driver |  |  |  |  |  |  |  |  |  |  |  |  | x |  |  |  |  |  |  |  |  |  |  |  |  |  |  |  |  | 2 |  |  |  |  |  |  |  |  | 2
P0540 | SICK RFID RFH621 reader |  |  | RFID_Sick_RFH621 |  |  |  |  |  |  |  |  |  | x |  |  |  |  |  |  |  |  |  |  |  |  |  |  |  |  |  |  |  |  |  |  |  | 1 |  | 1
 |  |  |  |  |  |  |  |  |  |  |  |  |  |  |  |  |  |  |  |  |  |  |  |  |  |  |  |  |  |  |  |  |  |  |  |  |  |  |  | 0
 |  |  |  |  |  |  |  |  |  |  |  |  |  |  |  |  |  |  |  |  |  |  |  |  |  |  |  |  |  |  |  |  |  |  |  |  |  |  |  | 0
 |  |  |  |  |  |  |  |  |  |  |  |  |  |  |  |  |  |  |  |  |  |  |  |  |  |  |  |  |  |  |  |  |  |  |  |  |  |  |  | 0
 |  |  |  |  |  |  |  |  |  |  |  |  |  |  |  |  |  |  |  |  |  |  |  |  |  |  |  |  |  |  |  |  |  |  |  |  |  |  |  | 0
 |  |  |  |  |  |  |  |  |  |  |  |  |  |  |  |  |  |  |  |  |  |  |  |  |  |  |  |  |  |  |  |  |  |  |  |  |  |  |  | 0
 |  |  |  |  |  |  |  |  |  |  |  |  |  |  |  |  |  |  |  |  |  |  |  |  |  |  |  |  |  |  |  |  |  |  |  |  |  |  |  | 0
 |  |  |  |  |  |  |  |  |  |  |  |  |  |  |  |  |  |  |  |  |  |  |  |  |  |  |  |  |  |  |  |  |  |  |  |  |  |  |  | 0
 |  |  |  |  |  |  |  |  |  |  |  |  |  |  |  |  |  |  |  |  |  |  |  |  |  |  |  |  |  |  |  |  |  |  |  |  |  |  |  | 0

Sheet: Assemblies
# | Part Num. | Part Name | Notes
1 | P0160 | 30x30 204mm profile 22,5deg cut
2 | P0165 | 30x30 138mm profile 22,5deg cut
3 | P0011 | 135 degree bracket | Use Screw_M6x14_ISO4762 with M6 washers and T-Nuts
# | Part Num. | Part Name | Notes
1 | P0155 | 30x30 339 mm profile flat cut
2 | P0016 | 135deg_small_braket M6 3holes | Use Screw_M6x14_ISO4762 with M6 washers and T-Nuts
3 | P0215 | Alu Profile square 10x10x1 259mm with holes | Insert threaded rivet M5 and use Screw_M6x20_ISO4762 with M6 washers and T-Nuts
4 | P0165 | 30x30 138mm profile 22,5deg cut | Use Screw_M6x14_ISO4762 with M6 washers and T-Nuts
# | Part Num. | Part Name | Notes
1 | P0170 | 30x30_200mm profile flat cut
2 | P0021 | 90 degree bracket | Use Screw_M6x14_ISO4762 with M6 washers and T-Nuts
3 | P0070 | 30x30 inner corner L nut | Screws for inner corner L nut
# | Part Num. | Part Name | Notes
1 | P0155 | 30x30 339 mm profile flat cut
2 | P0016 | 135deg_small_braket M6 3holes | Use Screw_M6x14_ISO4762 with M6 washers and T-Nuts
3 | P0165 | 30x30 138mm profile 22,5deg cut | Use Screw_M6x14_ISO4762 with M6 washers and T-Nuts
# | Part Num. | Part Name | Notes
1 | P0230 | Aluminum Profile L shape 30x20x1,5 98mm | Use Screw_M6x14_CS with M6 T-Nuts
2 | P0220 | Aluminum Profile L shape 30x20x1,5 250mm | Use Screw_M6x14_CS with M6 T-Nuts
# | Part Num. | Part Name | Notes
1 | P0415 | Drive support | Threaded rivet M5 in end hole, Screw_M6x14_ISO4762 with M6 washers and T-Nuts in first hole
2 | P0415 | Drive support | Threaded rivet M5 in mid hole, Screw_M6x14_ISO4762 with M6 washers and T-Nuts in first hole
3 | P0535 | PG Driver | Screw_M5x30_ISO4762
# | Part Num. | Part Name | Notes
1 | P0455 | Motor_Nidec_404_385_ right side
2 | P0460 | Motor_Nidec_404_385_left side
3 | P0470 | Encoder | Attach to motors
4 | P0290 | AGV_Soporte_motor_D | Use Screw_M6x14_CS (countersunk)
5 | P0295 | AGV_Soporte_motor_I | Use Screw_M6x14_CS (countersunk)
6 | P0300 | AGV_Rueda | Use Screw_M5x16_ISO4762 with M5 washer
# | Part Num. | Part Name | Notes
1 | P0435 | Balancing axel (tube 390x16mm)
2 | P0250 | 16mm axel corner clamp side a long | Use Screw_M6x14_ISO4762 with M6 washers and T-Nuts
3 | P0255 | 16mm axel corner clamp side b long | Use Screw_M6x14_ISO4762 with M6 washers and T-Nuts
4 | P0260 | Axel clamp | Use Screw_M6x14_ISO4762 with M6 washers and T-Nuts
# | Part Num. | Part Name | Notes
1 | P0175 | 30x30_60mm profile flat cut
2 | P0021 | 90 degree bracket | Use Screw_M6x14_ISO4762 with M6 washers and T-Nuts
3 | P0446 | Spring
# | Part Num. | Part Name | Notes
1 | P0430 | Clutch axel (tube 410x16mm)
2 | P0260 | Axel clamp | Use Screw_M6x14_ISO4762 with M6 washers and T-Nuts
3 | P0265 | Clutch-cam A | Use Screw_M6x35_ISO4762 with 2 x M6 washers and Nuts
4 | P0270 | Clutch-cam B | Use Screw_M6x35_ISO4762 with 2 x M6 washers and Nuts
5 | P0275 | Clutch axel cap
6 | P0280 | Clutch axel clamp A | Use Screw_M6x14_ISO4762 with M6 washers and T-Nuts
7 | P0285 | Clutch axel clamp B | Use Screw_M6x14_ISO4762 with M6 washers and T-Nuts
8 | P0390 | Clutch lever (100x5mm bar)
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

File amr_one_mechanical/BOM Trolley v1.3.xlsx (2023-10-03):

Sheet: BOM
BOM Trolly v1.3
 |  |  |  |  |  |  |  |  |  |  |  |  |  |  |  |  | 1 | 1 | 1 | 1 | 1 | 1 | 1
 |  |  |  |  |  | Parts group |  |  |  |  |  |  |  |  |  |  | Assemblies
Ref. Code | Part | Descripción | DIN | Name in CAD | File where design is | Brackets | Washers | Nuts | Screws | Profiles | 3D Printed Parts | Sheets | Other mechanical parts | Other | Price | Supplier Link | Base | Leg – Right | Leg – Left | Leg Support – Right | Leg Support – Left | Anchorage Set | Rail Set | TOTAL | Notas
P0011 | 135 degree bracket |  |  | 135 degree bracket type 002 | 135 degree bracket | x |  |  |  |  | x |  |  |  |  |  | 8 |  |  |  |  |  |  | 8
P0022 | 90 degree bracket (small) |  |  |  |  | x |  |  |  |  |  |  |  |  | 1.00 € | https://www.amazon.com/PZRT-Aluminum-Fastener-Standard-Extrusion/dp/B07H89R3QR | 8 | 8 | 8 | 2 | 2 |  |  | 28
P0035 | Washer M6 | Arandela M6 |  | Washer M6 |  |  | x |  |  |  |  |  |  |  |  | https://www.amazon.es/gp/product/B073GQLNL2 | 32 | 16 | 16 | 4 | 4 | 5 | 4 | 81
P0045 | Washer M8 |  |  | Washer M8 |  |  | x |  |  |  |  |  |  |  |  |  |  | 8 | 8 |  |  |  |  | 16
P0050 | T Nut M6 3030 | Tuerca en T para perfil 3030 M6 |  | T-slot nut M6 3030 |  |  |  | x |  |  |  |  |  |  |  | https://www.amazon.es/gp/product/B075WWWTYB/ref=crt_ewc_title_srh_5?ie=UTF8&psc=1&smid=A5QX2SUPA7LK7 | 32 | 16 | 16 | 4 | 4 | 4 | 4 | 80
P0060 | ISO4032_Hex_Nut_M6 |  |  |  |  |  |  | x |  |  |  |  |  |  |  |  |  |  |  |  |  | 1 |  | 1
P0065 | ISO4032_Hex_Nut_M8 |  |  | HEX Nut M8 |  |  |  | x |  |  |  |  |  |  |  |  |  | 2 | 2 |  |  |  |  | 4
P0070 | 30x30 inner corner L nut |  |  |  |  |  |  | x |  |  |  |  |  |  |  | https://www.amazon.com/uxcell-Interior-Connector-Aluminum-Extrusion/dp/B07VP59DY5 | 4 |  |  | 2 | 2 |  |  | 8
P0075 | Screws for inner corner L nut |  |  |  |  |  |  | x |  |  |  |  |  |  |  | https://www.amazon.es/Inoxidable-Tornillo-Prisionero-Hexagonal-Surtido/dp/B07PKMC57C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 | 8 |  |  | 4 | 4 |  |  | 16
P0125 | Screw_M6x14 HEX | Tornillo M6x16 hex |  | Screw_M6x14_ISO4762 |  |  |  |  | x |  |  |  |  |  |  | https://www.amazon.es/Xiedeai-Carbono-Hexagonales-Tornillo-Cabeza/dp/B07RMXVH98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 | 32 | 16 | 16 | 4 | 4 | 4 | 4 | 80
P0135 | Screw_M6x20 HEX |  |  | Screw_M6x20_ISO4762 |  |  |  |  | x |  |  |  |  |  |  | https://www.amazon.es/Tornillos-Sujetadores-Reborde-Inoxidable-Hexagonal/dp/B0746CFPZ8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 |  |  |  |  |  | 1 |  | 1
P0150 | Screw_M8x50 HEX HEAD |  |  | Bolt HEX M8x50 |  |  |  |  | x |  |  |  |  |  |  | https://www.amazon.es/Tornillos-de-cabeza-hexagonal-ISO-4017-M8x50-con-hex%C3%A1gono-externo-8-8-galvanizado-con-tuercas-ISO/dp/B086T124L8 |  | 2 | 2 |  |  |  |  | 4
P0160 | 30x30 204mm profile 22,5deg cut | Units: 4, Assembly: Base |  | 30x30_204mm_22.5deg profile | 30x30 profiles |  |  |  |  | x |  |  |  |  |  |  | 4 |  |  |  |  |  |  | 4
P0165 | 30x30 138mm profile 22,5deg cut | Units: 4, Assembly: Base |  | 30x30_138mm_22.5deg profile | 30x30 profiles |  |  |  |  | x |  |  |  |  |  |  | 4 |  |  |  |  |  |  | 4
P0156 | 30x30_109 mm profile flat cut | Units: 4, Assembly: Base |  | 30x30_109mm profile | 30x30 profiles |  |  |  |  | x |  |  |  |  |  |  | 4 |  |  |  |  |  |  | 4
P0171 | 30x30_339mm profile flat cut | Units: 2, Assembly: Base |  | 30x30_339mm profile | 30x30 profiles |  |  |  |  | x |  |  |  |  |  |  | 2 |  |  |  |  |  |  | 2
P0176 | 31x30_400mm profile flat cut | Units: 1+1, Assembly: Leg-Right, Leg-Left |  | 31x30_400mm profile | 31x30 profiles |  |  |  |  | x |  |  |  |  |  |  |  | 1 | 1 |  |  |  |  | 2
P0177 | 32x30_271mm profile flat cut | Units: 2+2, Assembly: Leg-Right, Leg-Left |  | 32x30_271mm profile | 32x30 profiles |  |  |  |  | x |  |  |  |  |  |  |  | 2 | 2 |  |  |  |  | 4
P0175 | 30x30_60mm profile flat cut | Units: 1+1, Assembly: LegSupport-Right / Left |  | 32x30_60mm profile | 30x30 profiles |  |  |  |  | x |  |  |  |  |  |  |  |  |  | 1 | 1 |  |  | 2
P0178 | 30x30_70mm profile flat cut | Units: 2+2, Assembly: LegSupport-Right / Left |  | 32x30_70mm profile | 30x30 profiles |  |  |  |  | x |  |  |  |  |  |  |  |  |  | 2 | 2 |  |  | 4
P0206 | Aluminum Profile L shape 30x30x1,5 with rail shape R | Rail Set |  | Rail – Right | Trolley v1.3 |  |  |  |  | x |  |  |  |  |  |  |  |  |  |  |  |  | 1 | 1
P0207 | Aluminum Profile L shape 30x30x1,5 with rail shape L | Rail Set |  | Rail – Left | Trolley v1.3 |  |  |  |  | x |  |  |  |  |  |  |  |  |  |  |  |  | 1 | 1
P0382 | 3mm washer | Rail Set |  | Big_Washer | Trolley v1.3 |  |  |  |  | x |  |  |  |  |  |  |  |  |  |  |  |  | 4 | 4
P0381 | Anchorage base sheet |  |  | Anchorage base | Trolley v1.3 |  |  |  |  |  |  | x |  |  |  |  |  |  |  |  |  | 1 |  | 1
P0391 | Steel trigger |  |  | Steel sheet | Trolley v1.3 |  |  |  |  |  |  | x |  |  |  |  |  |  |  |  |  | 1 |  | 1
P0322 | Anchorage front limit |  |  | Anchorage front limit | Trolley v1.3 |  |  |  |  |  | x |  |  |  |  |  |  |  |  |  |  | 1 |  | 1 | 3d printing part
P0405 | Rivet aluminum 4,2mm |  |  | 4,2mm_Rivet |  |  |  |  |  |  |  |  | x |  |  |  |  |  |  |  |  | 2 |  | 2
 |  |  |  |  |  |  |  |  |  |  |  |  |  |  |  |  |  |  |  |  |  |  |  | 0
 |  |  |  |  |  |  |  |  |  |  |  |  |  |  |  |  |  |  |  |  |  |  |  | 0
 |  |  |  |  |  |  |  |  |  |  |  |  |  |  |  |  |  |  |  |  |  |  |  | 0
 |  |  |  |  |  |  |  |  |  |  |  |  |  |  |  |  |  |  |  |  |  |  |  | 0
 |  |  |  |  |  |  |  |  |  |  |  |  |  |  |  |  |  |  |  |  |  |  |  | 0
 |  |  |  |  |  |  |  |  |  |  |  |  |  |  |  |  |  |  |  |  |  |  |  | 0
 |  |  |  |  |  |  |  |  |  |  |  |  |  |  |  |  |  |  |  |  |  |  |  | 0
 |  |  |  |  |  |  |  |  |  |  |  |  |  |  |  |  |  |  |  |  |  |  |  | 0

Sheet: Assemblies
# | Part Num. | Part Name | Notes
1 | P0160 | 30x30 204mm profile 22,5deg cut
2 | P0165 | 30x30 138mm profile 22,5deg cut
3 | P0011 | 135 degree bracket | Use Screw_M6x14_ISO4762 with M6 washers and T-Nuts
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

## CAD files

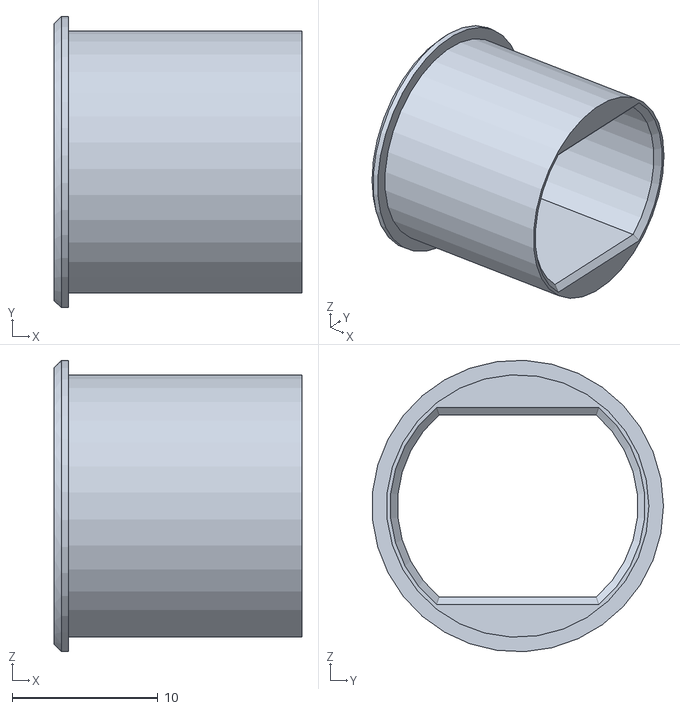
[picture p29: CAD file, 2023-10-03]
amr_one_mechanical/CAD designs/3D Printing/PinHook bottom cover v1.stl
17.0 x 20.0 x 20.0

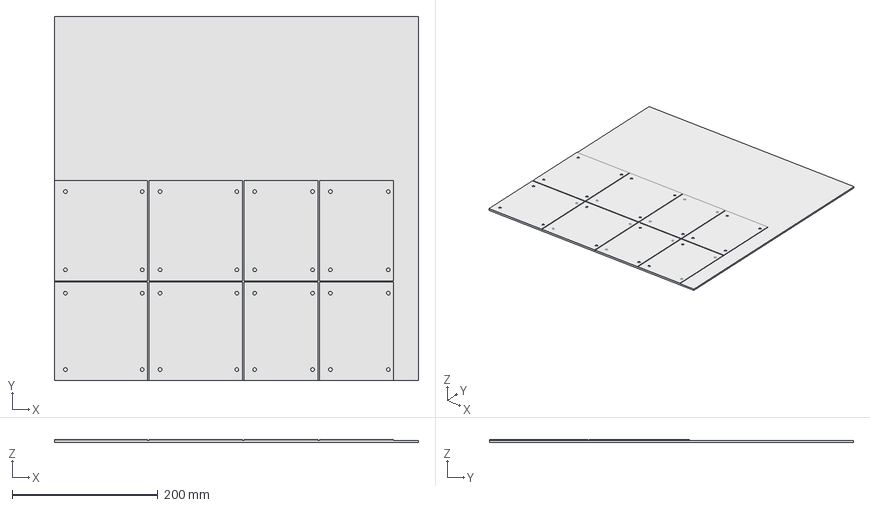
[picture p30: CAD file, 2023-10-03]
amr_one_mechanical/CAD designs/Sheets cut.FCStd
500.0 x 500.0 x 4.00 mm

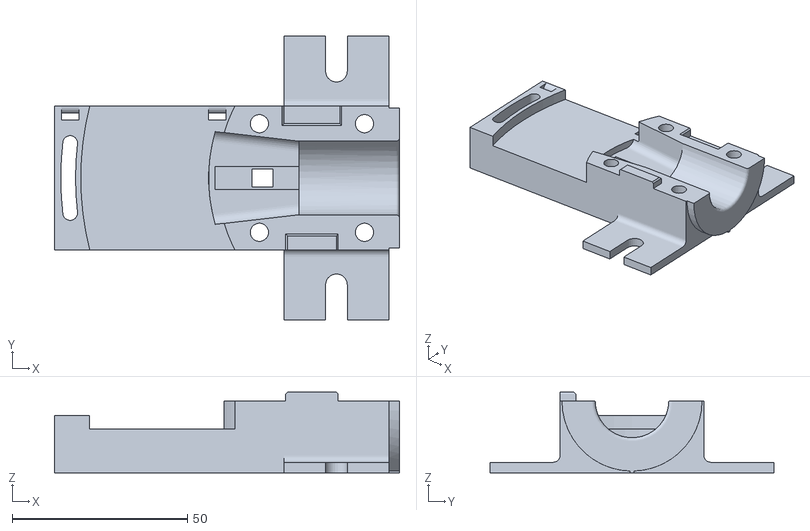
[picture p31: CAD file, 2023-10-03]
amr_one_mechanical/CAD designs/3D Printing/Pinhook container_v3.stl
98.5 x 81.0 x 23.0

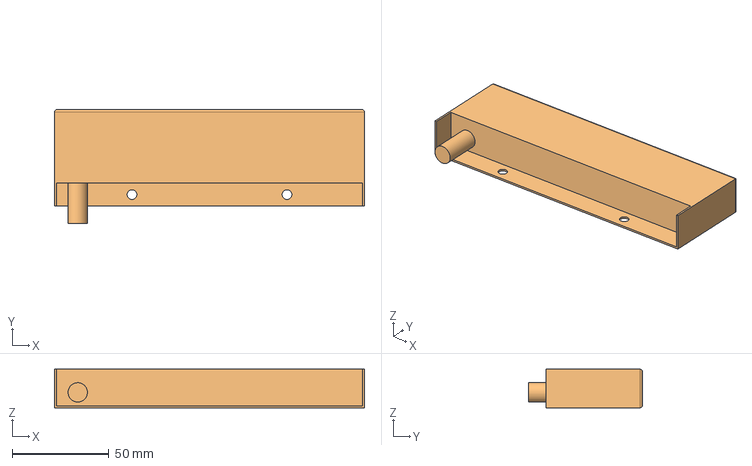
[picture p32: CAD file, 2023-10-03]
amr_one_mechanical/CAD designs/Parts/Magnetic Sensor Macome GS-4484.FCStd
160.0 x 59.0 x 20.0 mm
Magnetic Sensor Macome GS-4484

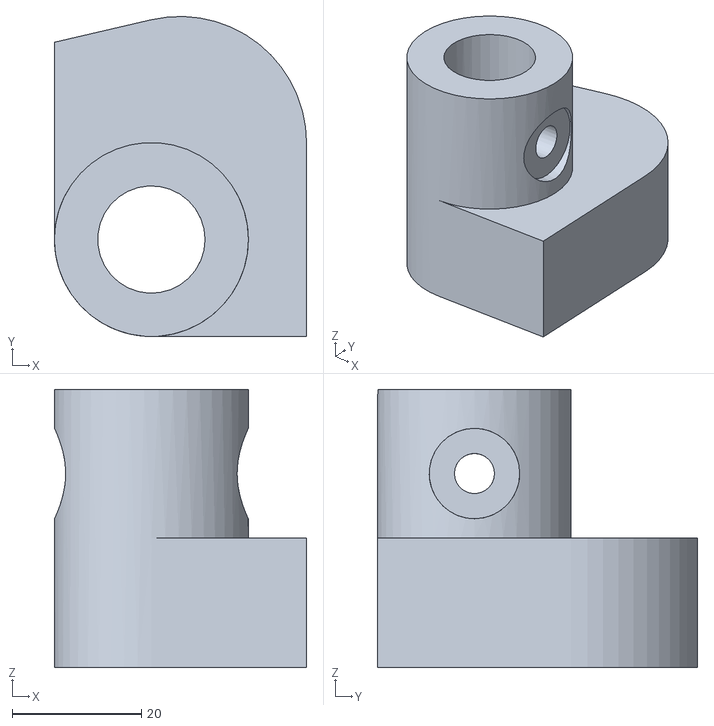
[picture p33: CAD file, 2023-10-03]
amr_one_mechanical/CAD designs/3D Printing/Clutch-cam A.stl
39.0 x 49.5 x 43.0

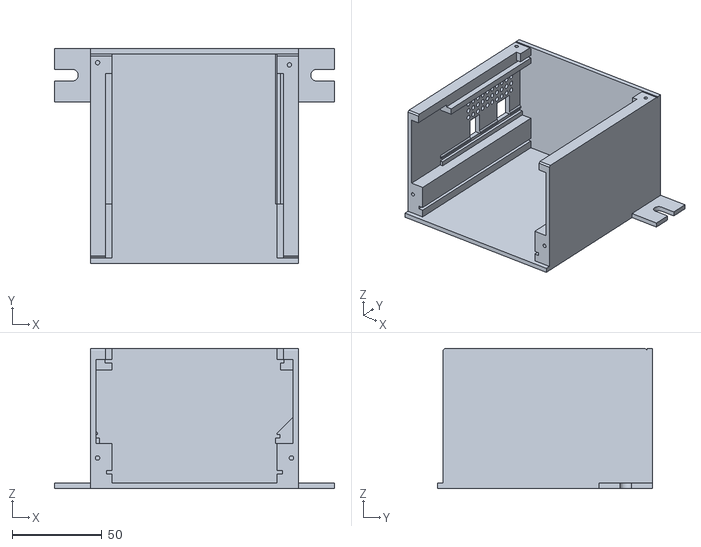
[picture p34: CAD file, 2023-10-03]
amr_one_mechanical/CAD designs/3D Printing/LLC_Box_Base_v3.stl
156.0 x 120.0 x 78.0

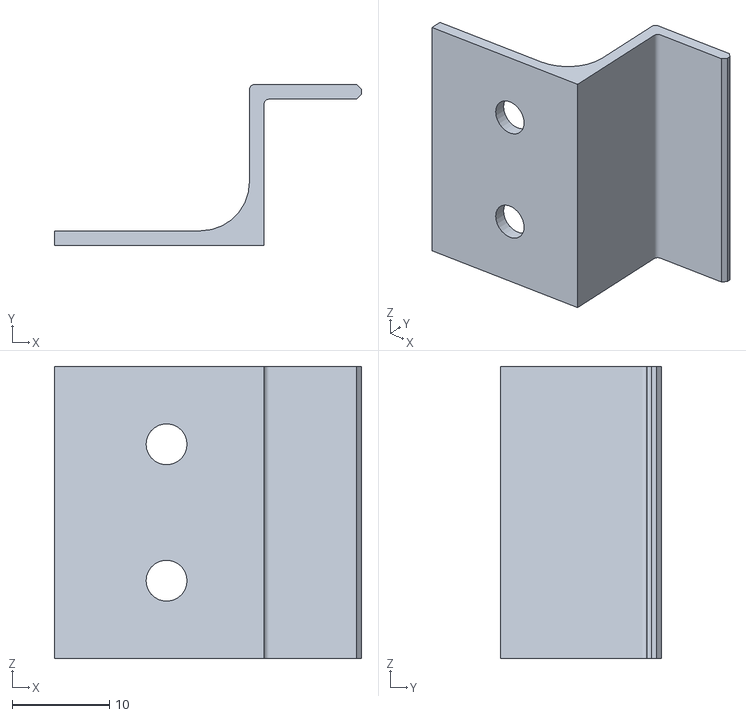
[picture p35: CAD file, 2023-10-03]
amr_one_mechanical/CAD designs/3D Printing/Bracket Front Laser type 002.stl
31.5 x 16.5 x 30.0

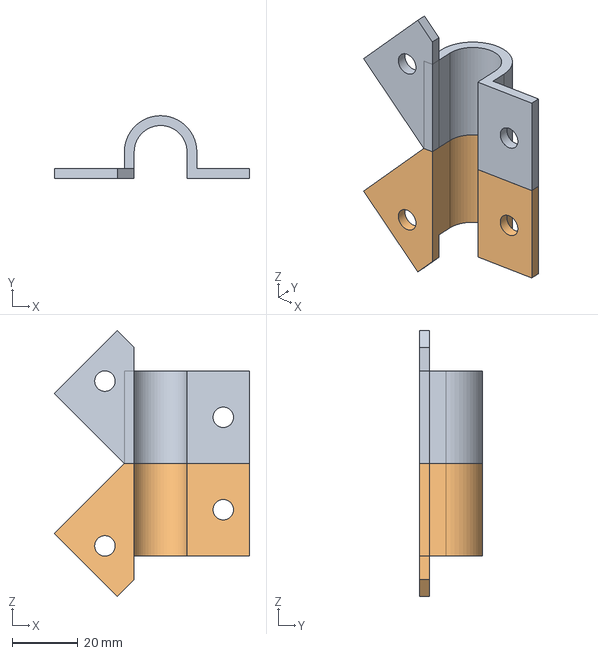
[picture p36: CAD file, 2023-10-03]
amr_one_mechanical/CAD designs/Parts/Clutch axel clamps.FCStd
59.2 x 19.0 x 80.6 mm
Clamp B
Clutch axel clamp B

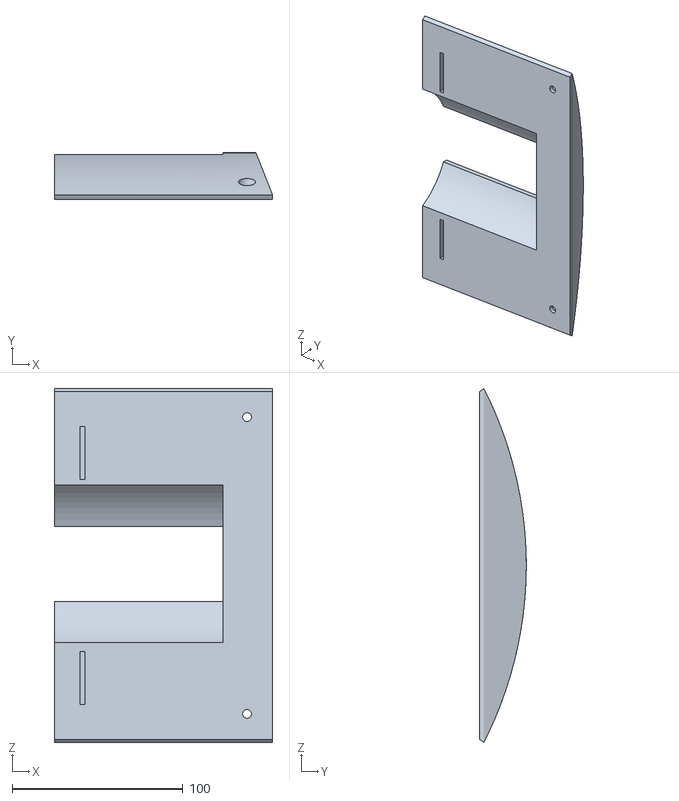
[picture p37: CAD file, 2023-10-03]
amr_one_mechanical/CAD designs/3D Printing/Front Top Cover.stl
128.0 x 27.3 x 207.6

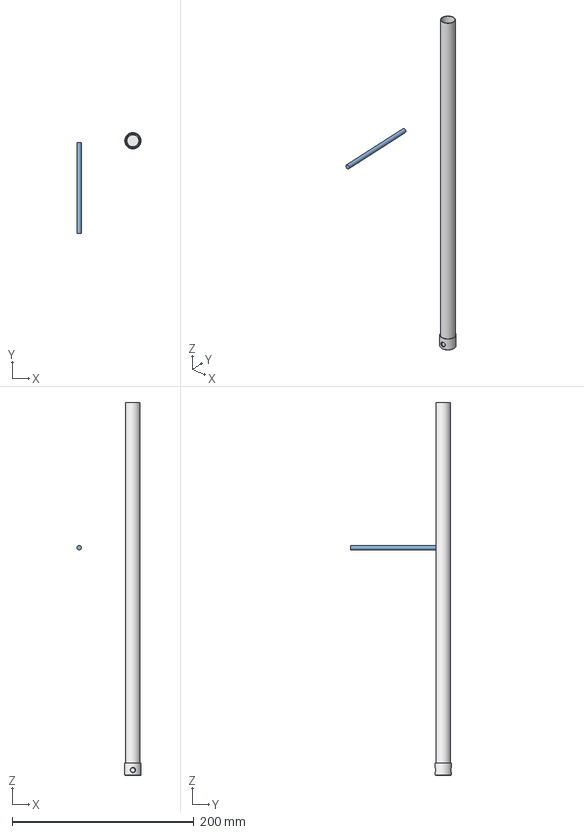
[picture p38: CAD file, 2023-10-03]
amr_one_mechanical/CAD designs/Parts/Clutch axel cup.FCStd
70.5 x 110.8 x 410.0 mm
Clutch axel cup 001
Clutch lever

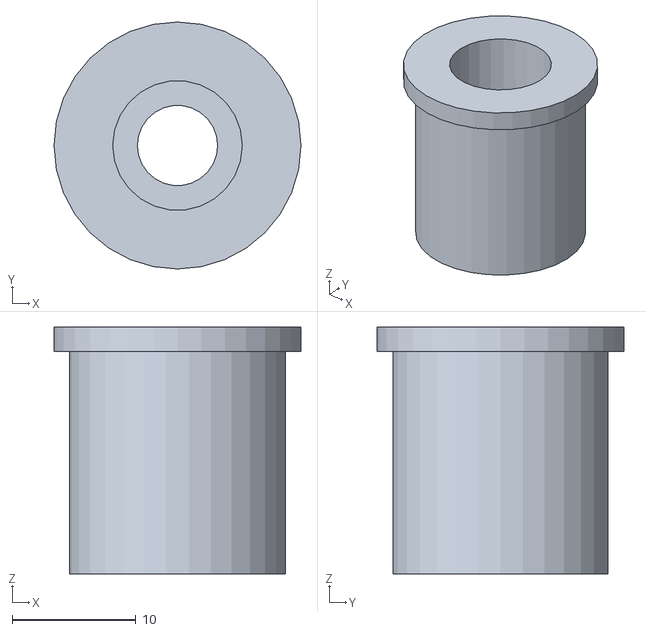
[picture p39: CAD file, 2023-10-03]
amr_one_mechanical/CAD designs/3D Printing/Anchor_front.stl
20.0 x 20.0 x 20.0

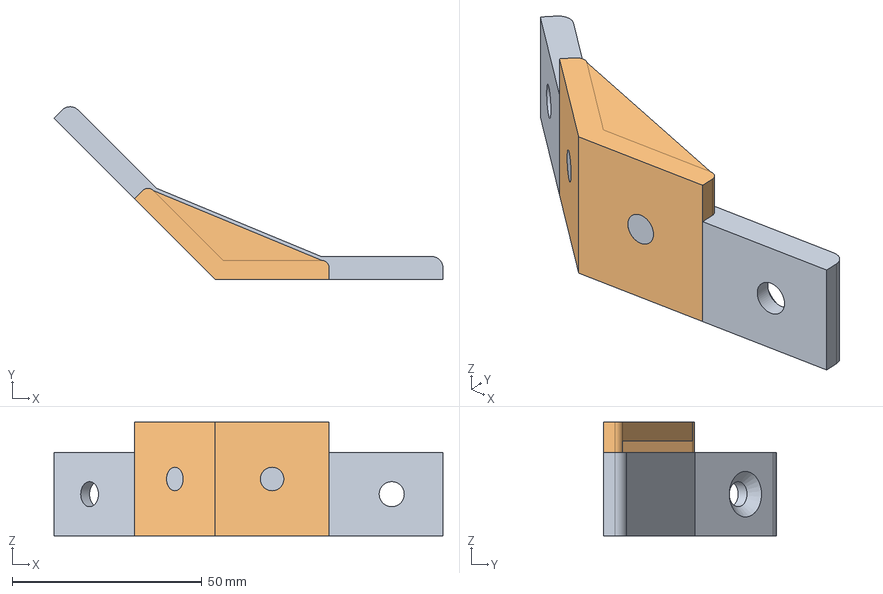
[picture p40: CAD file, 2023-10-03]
amr_one_mechanical/CAD designs/Parts/135 degree bracket.FCStd
102.4 x 45.4 x 30.0 mm
135deg bracket type 001
135deg bracket type 002
135deg bracket type 002.

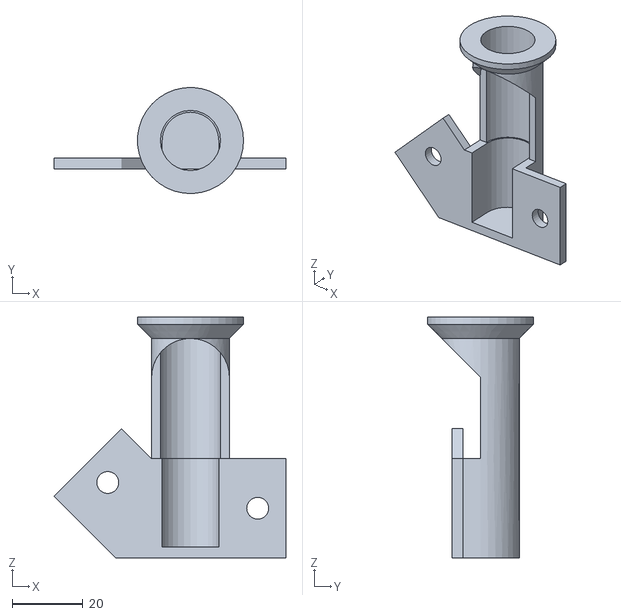
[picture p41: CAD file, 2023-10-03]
amr_one_mechanical/CAD designs/3D Printing/16mm axel corner clamp side a long.stl
65.6 x 30.0 x 68.0

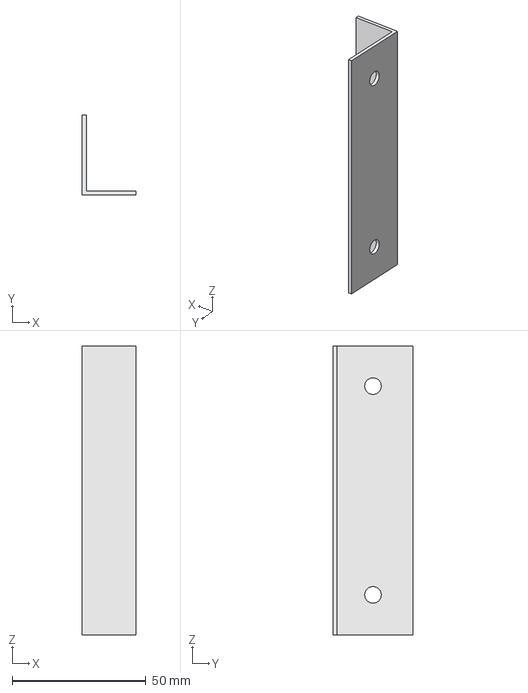
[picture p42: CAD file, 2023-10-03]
amr_one_mechanical/CAD designs/Parts/Aluminum Profiles.FCStd
20.0 x 30.0 x 108.0 mm

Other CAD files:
amr_one_mechanical/CAD designs/3D Printing/135deg_small_braket M6 3holes type 002.stl
amr_one_mechanical/CAD designs/Parts/AGV_Rueda_v3.FCStd
amr_one_mechanical/CAD designs/3D Printing/Clutch axel cap.stl
amr_one_mechanical/CAD designs/3D Printing/Front Bottom Cover.stl
amr_one_mechanical/CAD designs/3D Printing/135deg bracket type 002.stl
amr_one_mechanical/CAD designs/3D Printing/16mm axel corner clamp side b long.stl
amr_one_mechanical/CAD designs/3D Printing/30x30 corner bracket type 002.stl
amr_one_mechanical/CAD designs/3D Printing/AGV_Rueda_v3.stl
amr_one_mechanical/CAD designs/3D Printing/AGV_Soporte_motor_D_v1.stl
amr_one_mechanical/CAD designs/3D Printing/AGV_Soporte_motor_I_v4.stl
amr_one_mechanical/CAD designs/3D Printing/AMR_spring_support_v1.stl
amr_one_mechanical/CAD designs/3D Printing/Axel clamp.stl
amr_one_mechanical/CAD designs/3D Printing/Back bottom Cover.stl
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

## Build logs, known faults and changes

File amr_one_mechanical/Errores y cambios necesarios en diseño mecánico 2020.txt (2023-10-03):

- [ ] Remaches roscados m5 son 7mm de diametro
- [ ] remaches de perfiles a plancha laser son 4x8mm y las piezas de anclaje frontales, si son 3d llevan arandela m4 y remaches 4x10mm
- [ ] Tornillos soporte chasis vertical fino comprados mejores. Cabeza hexa llave del 8
- [ ] Tornillos anclaje motores a soporte no son M6x14 CS sino M6x20 como los de soporte chasis fino central vertical
- [ ] p0380a y b son cortas
- [ ] Pieza interruptor
- [ ] Plc, tornillos 5x30 son largos. Debe ser 5x25
- [ ] arandelas m6 anchas compradas están bien en general, mero hay por lo menos 10 a 15 que ha habido que cortarlas. Estrechas vendrían mejor en estos casos. Muy estrechas.
- [ ] mal calculadas dimensiones de fondo laser. Longitud de pieza total es 557mm, no 530, o dos piezas de 227 (no 2012) y una de 103mm
- [ ] En P0425, agujeros remache M4 son de 6,2mm
- [ ] bracket the RFID no coinciden agujeros con RFID. O modelo RFID mal o pieza, o precisiones de fabricación
- [ ] piezas 3d con agujero M6 que hay que aumentad diámetro 1mm: P0011, P0016, P0250, P0255, P0260, P0265, P0270
- [ ] No hay medidas en ensamblajes. Por ejemplo altura a la que queda el canal de haz láser o posición exacta de las barras verticales
- [ ] Las barras centrales superioer e inferior son cortas unos 3 o 4 mm no se si es pir imprecisión de cortes o por medidas mal tomadas
- [ ] Los tornillos de soporte de bateria M6x14cs podrían ser M5x12 para ahorrar referencias
- [ ] sensor banda medidas herróneas. Modificar modelo y pieza 3d frontal
- [ ] carril din puede ir de arriba abajo todo el alto del chasis. Junto a la parte del eje hay que recortar redondear.
- [ ] Piezas sujeción muelle, aliminio, 20x50mm con agujero 6mm en el centro y dobleces de 10mm a ambos lados
- [ ] Falta añadir a planos el pinhook

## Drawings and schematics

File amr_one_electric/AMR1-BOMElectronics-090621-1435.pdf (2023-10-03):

# BOM Electronics

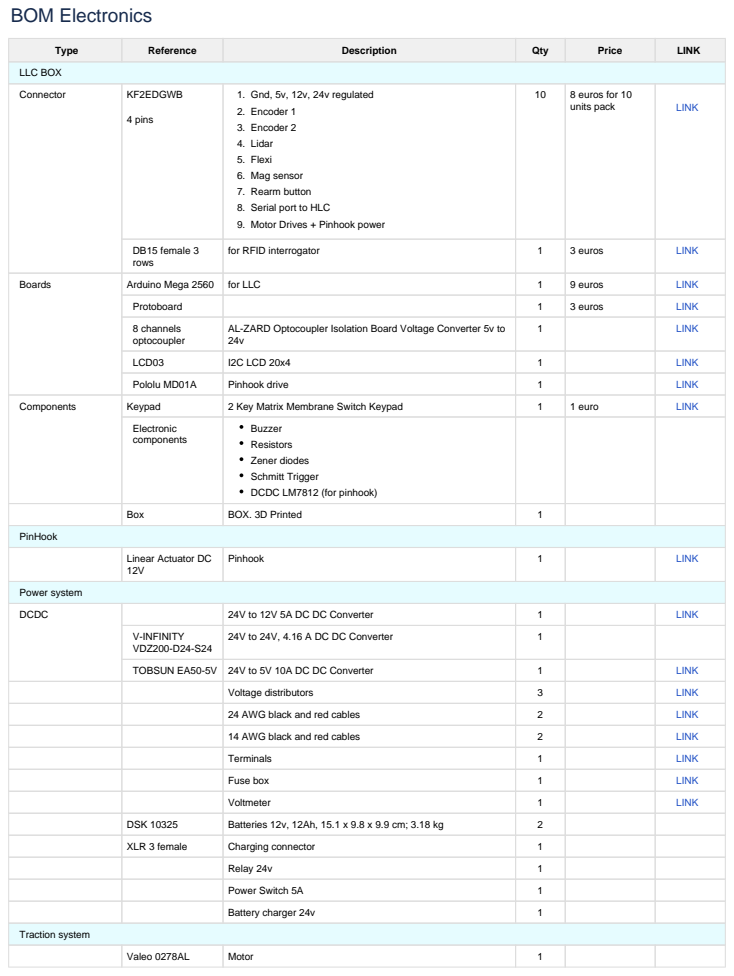
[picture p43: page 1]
Type; Reference; Description; Qty; Price; LINK; LLC BOX; Connector; KF2EDGWB; 4 pins; 8 euros for 10; units pack; DB15 female 3 rows; for RFID interrogator; 3 euros; Boards; Arduino Mega 2560 for LLC; 9 euros; Protoboard; 8 channels optocoupler; LCD03; I2C LCD 20x4; Pololu MD01A; Pinhook drive; Components; Keypad; 2 Key Matrix Membrane Switch Keypad; 1 euro; Electronic components; Box; BOX. 3D Printed; PinHook; Pinhook; Power system; DCDC; 24V to 12V 5A DC DC Converter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

Gnd, 5v, 12v, 24v regulated
Encoder 1
Encoder 2
Lidar
Flexi
Mag sensor
Rearm button
Serial port to HLC
Motor Drives + Pinhook power

AL-ZARD Optocoupler Isolation Board Voltage Converter 5v to

Buzzer
Resistors
Zener diodes
Schmitt Trigger
DCDC LM7812 (for pinhook)

Linear Actuator DC

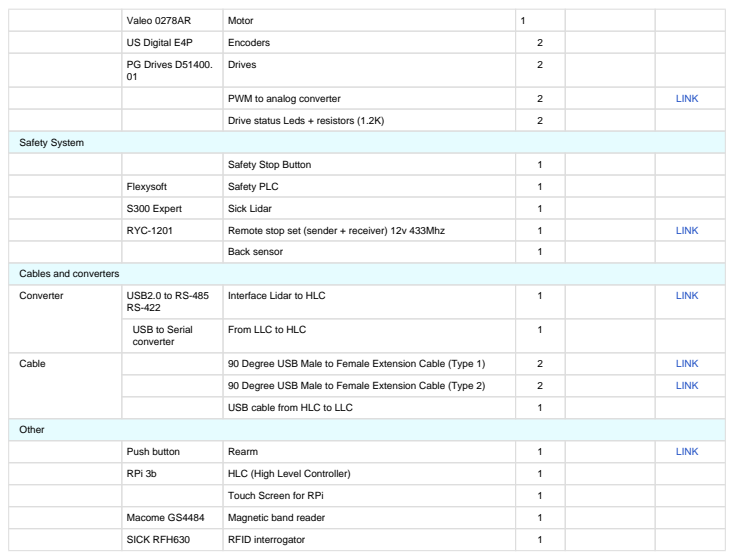
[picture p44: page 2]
Valeo 0278AR; Motor; US Digital E4P; Encoders; PG Drives D51400. 01; Drives; PWM to analog converter; LINK; Drive status Leds + resistors (1.2K); Safety System; Safety Stop Button; Flexysoft; Safety PLC; S300 Expert; Sick Lidar; RYC-1201; Remote stop set (sender + receiver) 12v 433Mhz; Back sensor; Converter; USB2.0 to RS-485; Interface Lidar to HLC; From LLC to HLC; Cable; 90 Degree USB Male to Female Extension Cable (Type 1); 90 Degree USB Male to Female Extension Cable (Type 2)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

Cables and converters

USB to Serial
converter

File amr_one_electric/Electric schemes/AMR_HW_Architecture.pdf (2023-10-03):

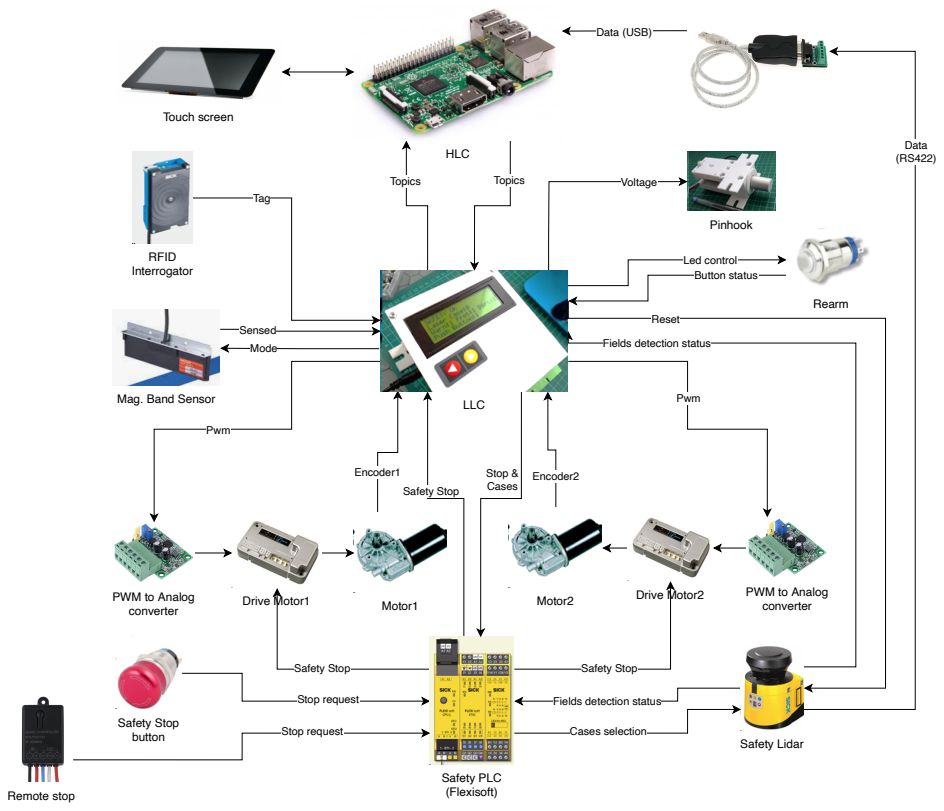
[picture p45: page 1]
Data (RS422); Safety Lidar; Pinhook; Encoder1; Motor1; Encoder2; Motor2; Drive Motor2 Drive Motor1; PWM to Analog; Stop request; Safety Stop button; Tag; RFID Interrogator; Safety Stop; Cases selection; Safety PLC (Flexisoft); Stop & Cases; Pwm; Reset; Mode; Voltage; Led control; Topics; LLC; Sensed; Button status; Rearm; HLC; Touch screen; Data (USB); Remote stop

Fields detection status

Mag. Band Sensor

converter PWM to Analog
converter

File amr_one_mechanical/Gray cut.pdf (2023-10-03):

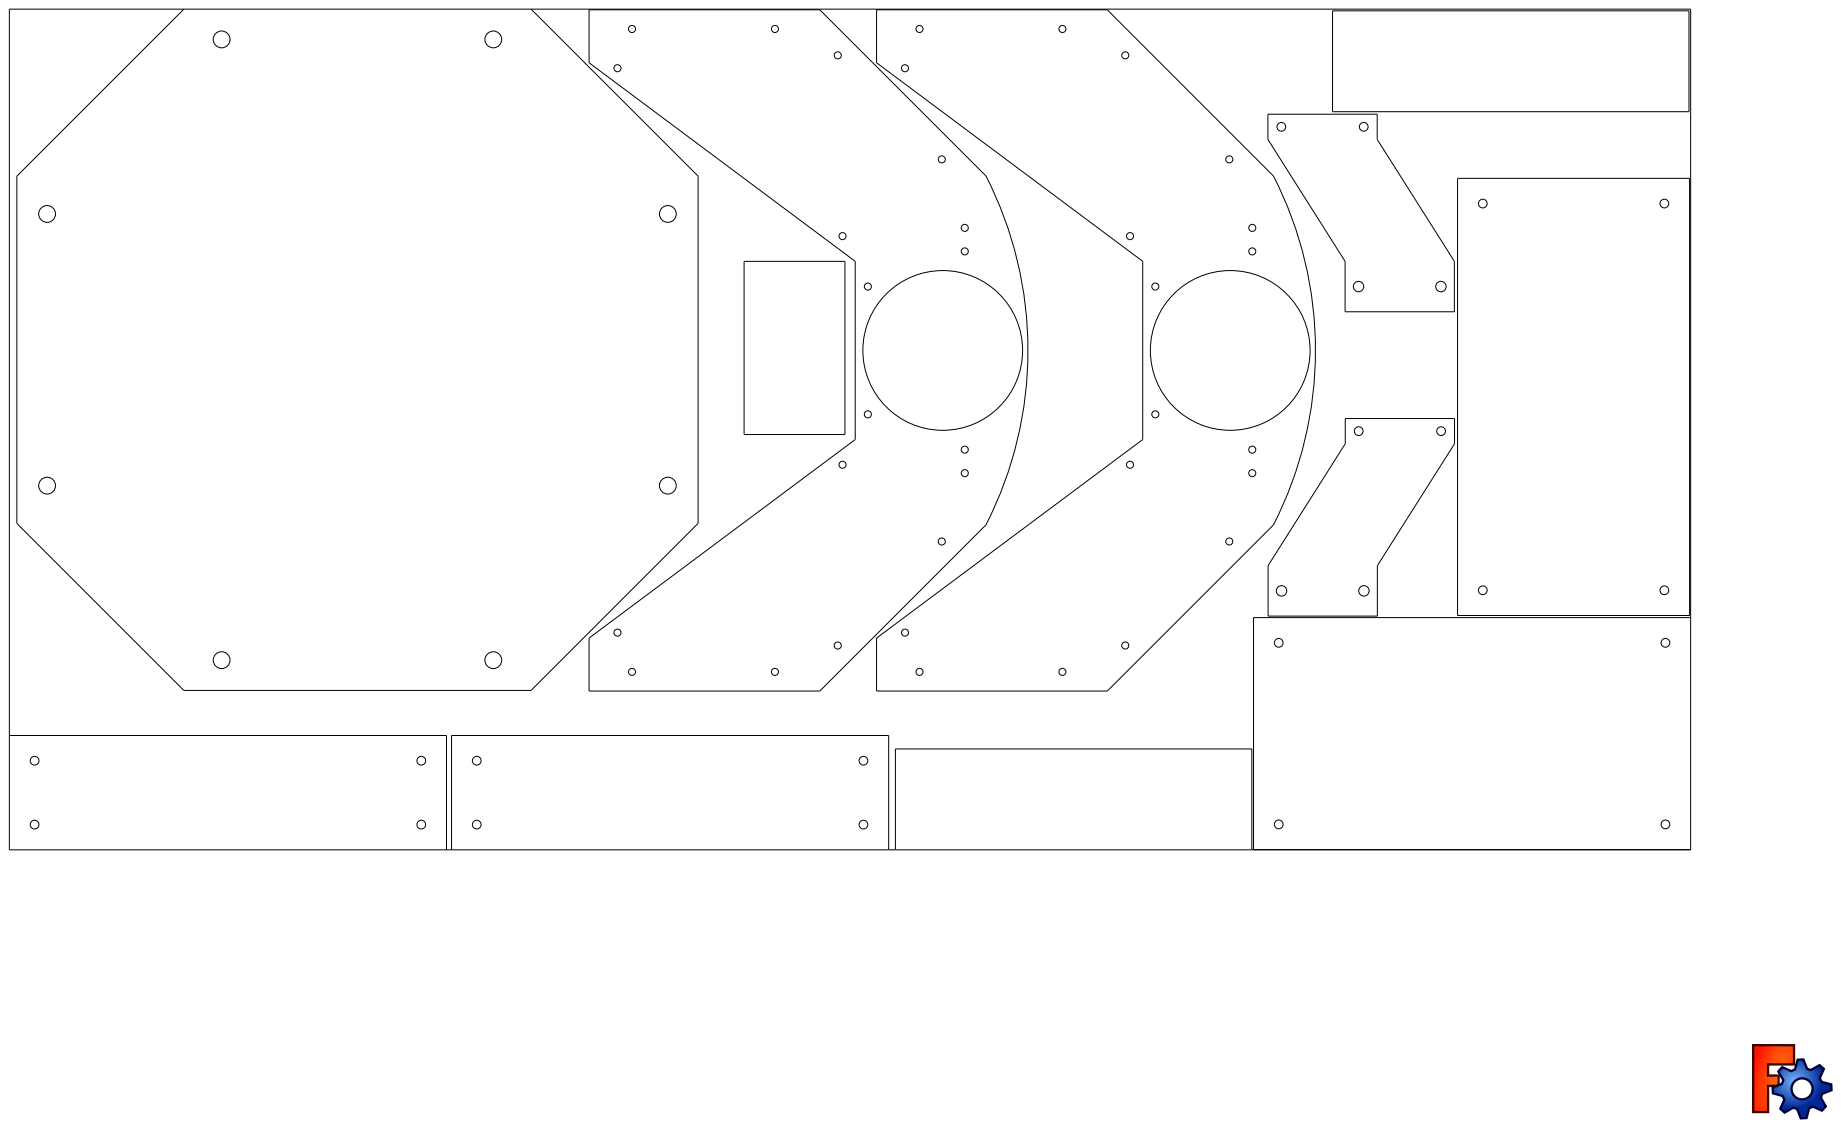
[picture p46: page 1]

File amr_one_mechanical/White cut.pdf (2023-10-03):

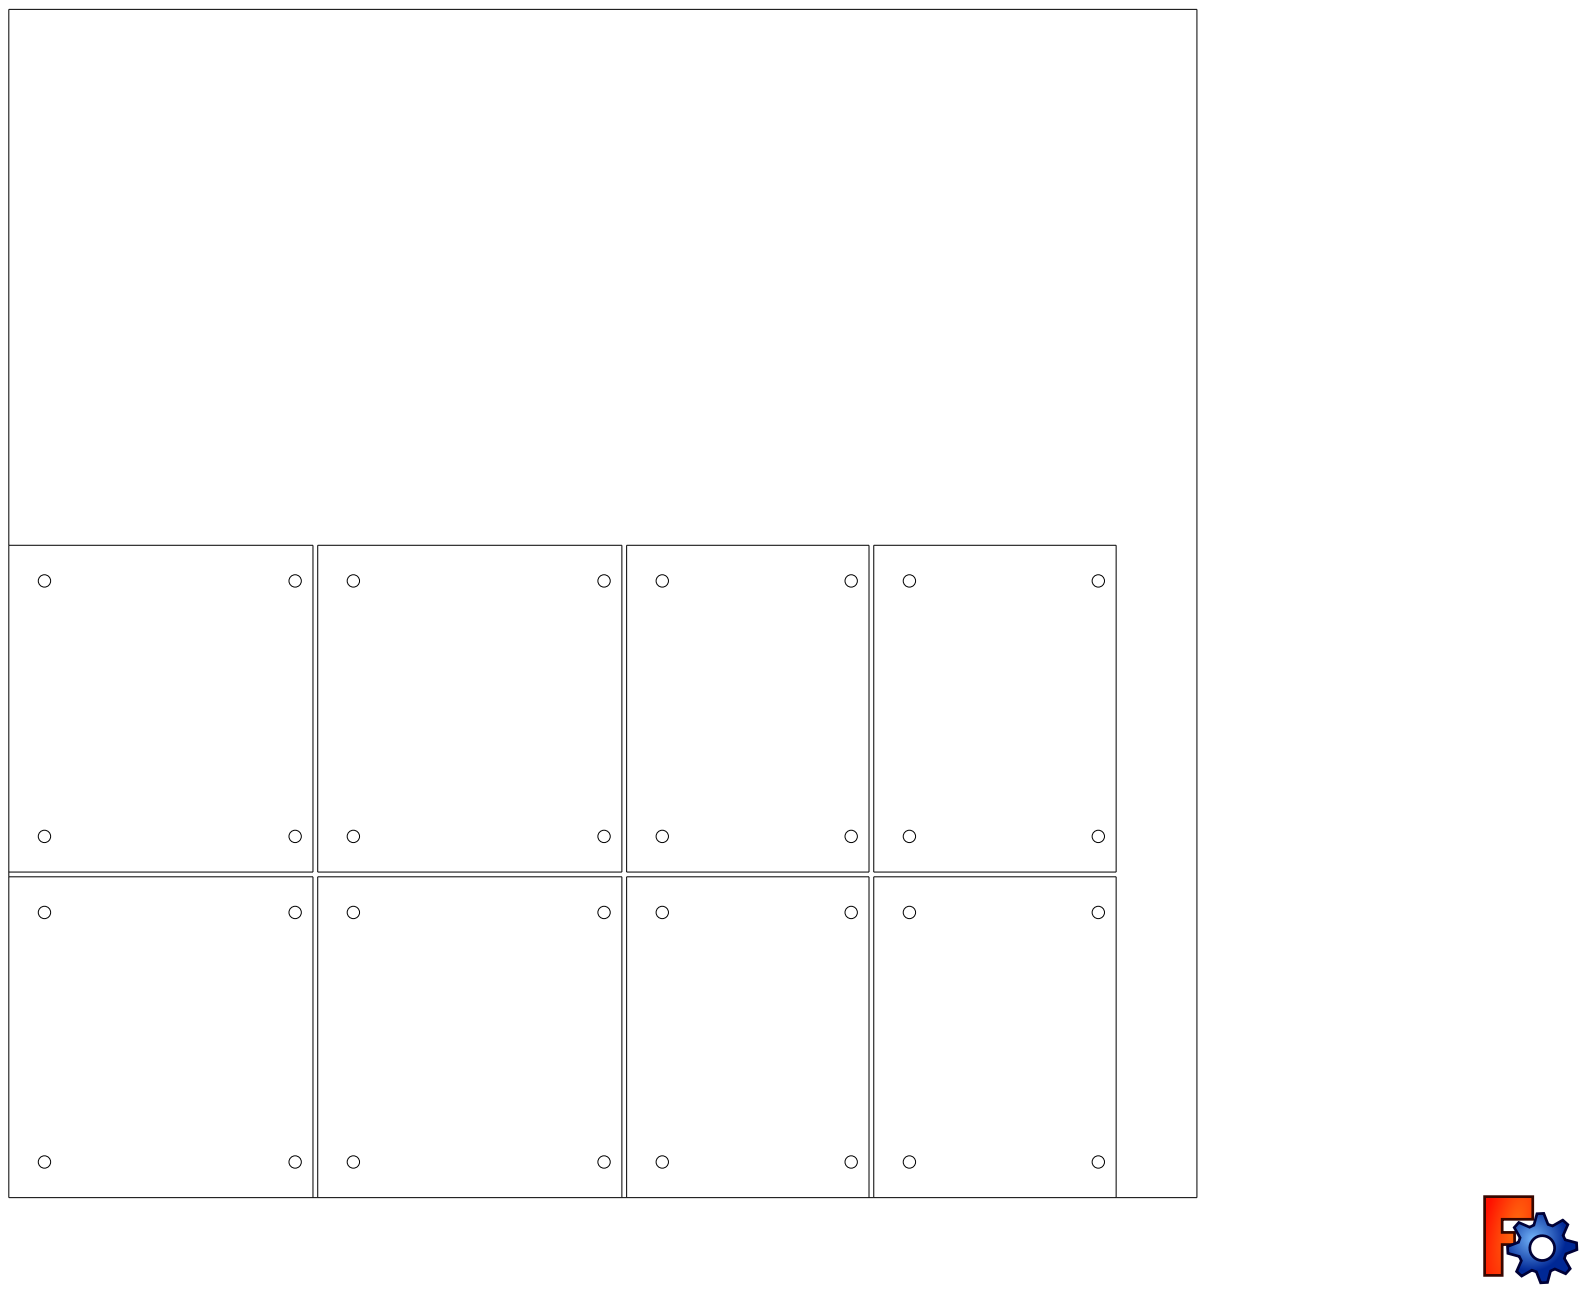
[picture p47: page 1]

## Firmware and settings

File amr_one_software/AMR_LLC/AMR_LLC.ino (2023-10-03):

/*
 * Program AMR-board.
 * Used for the low level control of the AMR
 * by Alejandro Alonso Puig. April 2022
 * 
 * 
 * Copyright 2022 Alejandro Alonso Puig. All Rights Reserved.
 * 
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
 * Versions
 * 0.01: Only LCD
 * 0.02: added keypad
 * 0.03: added PID control over motor and Encoder measurement
 * 0.04: Changed PID library with this one: FastPID: https://github.com/mike-matera/FastPID 
 * 0.05: Two motors with PID
 * 0.06: Buzzer added
 * 0.07: Safety stop implemented
 * 0.08: Pinhook implemented
 * 0.09: Lidar management implemented
 * 0.10: LCD screens + Adaptation to AMR motors (PWM from 0 to 250 duty, being 127:stop, 0:max reverse and 255:max forward. Freq betweern 1khz and 3khz
 * 0.11: Improve PID management (timings and stable readings for encoders) using timer1 interrupts
 * 0.12: Improvement on PID to include global setpoint and deviation control
 * 0.13: Incorporated signals from lidar, mag sensor, safety PLC, rearm button 
 * 0.14: Incorporated basic magnetic guidance with PID (defective version in PIDs)
 * 0.15: Deep review on PID to control limits, strange behaviors,...
 * 0.16: New deep review of PID after Drive configuration without automatic switch off at stop
 * 0.17: Added LCD screen with aditional data (Magnetic guidance, RFID tag code, data from Lidar signals and safety, time on measured) 
 * 0.18: Deviation control in a smoother way
 * 0.19: Some bugs corrected in deviation control
 * 0.20: RFID interrogator integration
 * 0.21: ROSSERIAL integration. Jira issue AMR-95 (not finished)
 * 0.22: 2 keys keypad + control of LCD screens + some cleaning on code
 * 0.23: Implementation of bip-bip sounds when Lidar detects objects in its protective field (2Hz bip) or warning field (1Hz bip). Buzzer_warnings() function
 * 0.24: Delay of 20 seconds until buzzer warning related to Lidar, as Lidar needs 20 second to boot up completely
 * 0.25: Added buzzer warning (beep every 4 seconds) if safety stop button (local or remote) is active
 * 0.26: Review Magnetic Guidance
 * 0.27: RFID tags actions implemented
 * 0.28: Mag band by default, added control of pinhook via serial
 * 0.29: ROSSERIAL integration. Jira issue AMR-247. Deactivated serial interface with user (see Jira issue AMR-248)
 */

#define VERSION 0.29
 
// PINS MAP

// PWM/Digital (02..13)
#define PIN_ENCODER1A        3 //Input.   Pins where connected encoder. First should have interrupt (Options: 2, 3, 18, 19, 20, 21 in Mega)
#define PIN_ENCODER1B        4 //Input.   Pins where connected encoder. 
#define PIN_ENCODER2A        2 //Input.   Pins where connected encoder. First should have interrupt (Options: 2, 3, 18, 19, 20, 21 in Mega)
#define PIN_ENCODER2B        5 //Input.   Pins where connected encoder.
#define PIN_MOTOR1_PWM       6 //Output.  Motor 1 PWM output. Default freq. is 490 Hz, except pin 4 and 13 whose default frequency is 980Hz.
#define PIN_MOTOR2_PWM       7 //Output.  Motor 2 PWM output. Default freq. is 490 Hz, except pin 4 and 13 whose default frequency is 980Hz.
#define PIN_BUZZER           8 //Output.  Buzzer
#define PIN_KBD_Inc          9 //Output.  Keyboard. Increment button
#define PIN_KBD_Dec         10 //Output.  Keyboard. Decrement button
#define PIN_KBD_CMN         11 //Output.  Keyboard. common

//Digital (22..53)
#define PIN_SAFETYSTOP      22 //Input.   Safety Stop input (From Safety PLC Flexysoft) 1=Safety stop, 0=No Safety stop
#define PIN_BUTTON          23 //Input.   Multipurpose button (Rearm button)
#define PIN_MOTORS_ACTIVE   24 //Output.  Motor Drives active (Indicates if Motor Drives should be active (1) or not (0). To Safety PLC)
#define PIN_LIDAR_WARNING   25 //Input.   Lidar Warning Field compromised (From Lidar)
#define PIN_LIDAR_PROTECT   26 //Input.   Lidar Protective Field compromised (From Lidar)
#define PIN_LIDAR_DIRTY     27 //Input.   Lidar Dirty lens warning (From Lidar)
#define PIN_LIDAR_RESET     28 //Output.  Lidar Reset
#define PIN_LIDAR_CASEBIT0  29 //Output.  Lidar Case bit0 (To Safety PLC. It activates in Lidat via EFI)
#define PIN_LIDAR_CASEBIT1  30 //Output.  Lidar Case bit1 (To Safety PLC. It activates in Lidat via EFI)
#define PIN_PINHOOK_DIR0    31 //Output.  Pinhook direction bit0
#define PIN_PINHOOK_DIR1    32 //Output.  Pinhook direction bit1
#define PIN_MAG_SEL1        33 //Output.  Magnetic band sensor. Selector signal 1
#define PIN_MAG_SEL2        34 //Output.  Magnetic band sensor. Selector signal 2
#define PIN_MAG_GATE        35 //Input.   Magnetic band sensor. Negative logic. LOW:Band detected, HIGH:Not detected
#define PIN_BUTTON_LED      36 //Output.  Multipurpose button led

//Analog (A0..A15)
#define PIN_MAG_DEV         A0 //Input.  Magnetic band sensor. Deviation. Analog

 
//ROS integration
#include <ros.h>              //rosserial library https://github.com/frankjoshua/rosserial_arduino_lib
#include <std_msgs/String.h>
#include <std_msgs/Float32.h>
#include <std_msgs/UInt16.h>
ros::NodeHandle  nh;
std_msgs::Float32 velocity_lin_msg;
std_msgs::Float32 velocity_ang_msg;
std_msgs::UInt16 safety_status_msg;
std_msgs::String rfid_tag_msg;
ros::Publisher pub_velocity_lin("velocity_lin", &velocity_lin_msg);
ros::Publisher pub_velocity_ang("velocity_ang", &velocity_ang_msg);
ros::Publisher pub_safety_status("safety_status", &safety_status_msg);
ros::Publisher pub_rfid_tag("rfid_tag", &rfid_tag_msg);
char rfidcode[5] = "    ";

  
#include <Key.h>
#include <Keypad.h>           //Keypad library https://playground.arduino.cc/Code/Keypad/

#include <Wire.h>             //I2C Library
#include <LCD03.h>            //LCD screen https://github.com/andatche/arduino-lcd03

#include <Encoder.h>          //Encoder library https://www.pjrc.com/teensy/td_libs_Encoder.html
#include <FastPID.h>          // PID library https://github.com/mike-matera/FastPID
#include <uptime_formatter.h> // Uptime Library. https://github.com/YiannisBourkelis/Uptime-Library
#include <uptime.h>

#define PID_Interrupt_ms  70  //Time in ms between two interrupts to evaluate PID
#define MOTORS_PWM_STOP  127  //PWM at which motors stops
//#define MOTORS_MinSetPoint  0   //Minimum setpoint for motors (below this value could become unstable or stop in low PWM values)
//#define MOTORS_MaxSetPoint  800  //Maximum setpoint for motors (above it could be to fast for the application) 
//#define MOTORS_MaxDeviation 83.6875 //Maximum deviation allowd (equivalent to 1rad/s)
#define MOTORS_MaxDeviation 13 //Maximum deviation allowed (equivalent to 10%) for Magnetic guidance
#define MOTORS_MaxAngular_Velocity 4.00 //Maximum angular velocity in rad/s
//#define MOTORS_MaxAngular_Velocity 3.14 //Maximum angular velocity in rad/s
#define MOTORS_MaxLinear_Velocity 1.0 //Maximum linear velocity in m/sg
#define MAG_SETPOINT  640 //Setpoint for magnetic sensor

//RFID Tags
#define RFID_ACTION_PINHOOK_UP  1
#define RFID_ACTION_PINHOOK_DWN 2
#define RFID_ACTION_FAST_SPEED  3
#define RFID_ACTION_SLOW_SPEED  4
#define RFID_ACTION_ROTATE180   5
struct tag_and_actions
{
  String  tag;
  byte    action;
  String  description;
};
tag_and_actions RFID_tag [] = { {"1D05", RFID_ACTION_PINHOOK_UP   ,"Pinhook UP" },
                                {"E140", RFID_ACTION_PINHOOK_DWN  ,"Pinhook DW"},
                                {"416C", RFID_ACTION_FAST_SPEED   ,"Fast Speed" },
                                {"1D04", RFID_ACTION_SLOW_SPEED   ,"Slow Speed" },
                                {"48A8", RFID_ACTION_ROTATE180    ,"Rotate 180" }};
tag_and_actions RFID_read; //RFID tag read

#include "pitches.h"          //pitch values for typical notes (buzzer) https://www.arduino.cc/en/Tutorial/BuiltInExamples/toneMelody
int melody[] = {NOTE_C4, NOTE_G3, NOTE_G3, NOTE_A3, NOTE_G3, 0, NOTE_B3, NOTE_C4}; // notes in the melody
int noteDurations[] = {4, 8, 8, 4, 4, 4, 4, 4};  // note durations: 4 = quarter note, 8 = eighth note, etc.

//Timer variables for ROS topic publishing
long ROSpub_t2 = 0;
long ROSpub_t1 = 0;
long ROSpub_t_interval = 1000; //Milliseconds between publishes

//Timer variables for Buzzer warnings
long Buzzer_t2 = 0;
long Buzzer_t1 = 0;
long Buzzer_t_interval = 0; 
bool Buzzer_warnings_allowed = false; //Allow or not the buzzer warning

//Timer variables for Magnetic guidance use
long Mag_t1 = 0;
long Mag_t2 = 0;
long Mag_t_interval = PID_Interrupt_ms; //Milliseconds between two PID loops

//Timer variables for RFID use
long RFID_t1 = 0;
long RFID_t2 = 0;
long RFID_t_interval = 500; //Milliseconds between two RFID reads

//Timer variables for external commands check use
long ExtCmd_t1 = 0;
long ExtCmd_t2 = 0;
long ExtCmd_t_interval = 500; //Milliseconds between external commands check

//Timer variables for LCD refresh use
long LCD_t1 = 0;
long LCD_t2 = 0;
long LCD_t_interval = 500; //Milliseconds between LCD refresh
byte LCD_Scr_Num = 0; //LCD Screen to show
byte LCD_Max_Scr_Num = 4;

//For Keyboard
char customKey; //Key from keypad (instant)
char KbdKey; //Key from keyboard

byte LidarCase = 0; // (0:Short case, 1:Long case, 2:Park mode, 3:No detection) 
bool MagGuidance_Active = false; //Indicates if magnetic guidance control is active or not
byte magnetic_mode = 0; //Magnetic band mode 0:Straight, 1:Left, 2:Right

bool RFID_Active = true; //Indicates if RFID control is active or not
byte Lidar_ready = false; //Indicates when Lidar is ready after booting up

long timer1_counter; //For Timer interrupt

bool PinHook_UP = false; // If Pinhook is UP or not

//BEGIN Keypad 
  const byte ROWS = 2; 
  const byte COLS = 1;  
  char hexaKeys[ROWS][COLS] = {'<', '>'};  
  byte rowPins[ROWS] = {PIN_KBD_Dec, PIN_KBD_Inc}; //Pins where keypad is connected
  byte colPins[COLS] = {PIN_KBD_CMN};    //Pins where keypad is connected
  Keypad customKeypad = Keypad(makeKeymap(hexaKeys), rowPins, colPins, ROWS, COLS); 
//END Keypad


LCD03 lcd;                                  // Create new LCD03 instance

//BEGIN PID_Control for drive motors
  bool  Motors_active_status = false;       //Indicates if motors are active or not. Changing this value changes the value sent to safety PLC
  bool  set_stop = false;                
  int16_t Motor1_feedback = 0;                //Speed varible measured by encoders (Motor 1)
  int16_t Motor2_feedback = 0;                //Speed varible measured by encoders (Motor 2)
  int16_t Motors_setpoint = 0;                //SetPoint for the Pid Controllers of motors measured in cycles (signal measured by encoders) per every 20ms (time PID interruptions)
  int16_t Motor1_setpoint = 0;                //SetPoint for the Pid Controllers of motor 1 measured in cycles (signal measured by encoders) per every 20ms (time PID interruptions)
  int16_t Motor2_setpoint = 0;                //SetPoint for the Pid Controllers of motor 2 measured in cycles (signal measured by encoders) per every 20ms (time PID interruptions)

  uint8_t PID_output1 = 0;                  //Output from PID algorithm (accumulated error)
  uint8_t PID_output2 = 0;                  //Output from PID algorithm (accumulated error)
  uint8_t Motor1_PWM = MOTORS_PWM_STOP;     //PWM value for motor drive 1
  uint8_t Motor2_PWM = MOTORS_PWM_STOP;     //PWM value for motor drive 2
  float Kp1=0.02, Ki1=0.03, Kd1=0.00, Hz1=1000/PID_Interrupt_ms;    //Specify initial tuning parameters Motor 1. Kp,Ki, Kd [0.00390625 to 255]
  float Kp2=0.02, Ki2=0.02, Kd2=0.00, Hz2=1000/PID_Interrupt_ms;    //Specify initial tuning parameters Motor 2. Kp,Ki, Kd  [0.00390625 to 255]
  float Kpm=0.05, Kim=0.00, Kdm=0.20, Hzm=1000/PID_Interrupt_ms;    //Specify initial tuning parameters Mag guidance (angular velocity). Kp,Ki, Kd  [0.00390625 to 255]
  int output_bits = 8;
  bool output_signed = false;
  FastPID Motor1_PID(Kp1, Ki1, Kd1, Hz1, output_bits, output_signed); //PID for Motor 1 (right)
  FastPID Motor2_PID(Kp2, Ki2, Kd2, Hz2, output_bits, output_signed); //PID for Motor 2 (left)
  FastPID Mag_PID(Kpm, Kim, Kdm, Hzm, output_bits, output_signed);    //PID for magnetic guidance
//END PID_Control

//For velocities
float Global_Linear_Velocity = 0; 
float Global_Angular_Velocity = 0;
float Global_Linear_Velocity_pre = 0;  //previous value
float Global_Angular_Velocity_pre = 0;
int16_t Angular_Velocity_Int = 0; //Temporary variable used in Magnetic guidance


//BEGIN Encoder
  // Change these two numbers to the pins connected to your encoder.
  //   Best Performance: both pins have interrupt capability
  //   Good Performance: only the first pin has interrupt capability
  //   Low Performance:  neither pin has interrupt capability
  Encoder Encoder1(PIN_ENCODER1A, PIN_ENCODER1B);   //Pins where connected encoder. First should have interrupt (Options: 2, 3, 18, 19, 20, 21 in Mega)
  Encoder Encoder2(PIN_ENCODER2A, PIN_ENCODER2B);   //Pins where connected encoder. First should have interrupt (Options: 2, 3, 18, 19, 20, 21 in Mega)
  //   avoid using pins with LEDs attached
//END Encoder


//FUNCTIONS

#define STATUS  2
#define UP      1
#define DOWN    0
#define STOP    3
#define ON      1
#define OFF     0

byte PinHook (byte command) {
  //Allows moving up or down the pinhook and asking for status (up or down)
  switch (command) {
      case STATUS:
        return (PinHook_UP); //1 up, 0 down
        break;
      case UP:
        digitalWrite(PIN_PINHOOK_DIR0, HIGH);
        digitalWrite(PIN_PINHOOK_DIR1, LOW);
        PinHook_UP = true;
        break;
      case DOWN:
        digitalWrite(PIN_PINHOOK_DIR0, LOW);
        digitalWrite(PIN_PINHOOK_DIR1, HIGH);
        PinHook_UP = false;
        break;
      default:
        // if nothing else matches is stop
        digitalWrite(PIN_PINHOOK_DIR0, LOW);
        digitalWrite(PIN_PINHOOK_DIR1, LOW);
      break;
    }
}


byte GetLidarStatus () {
  //Returns status of Lidar in a byte, being b0 the warning field status, b1 the protective field and b2 the dirty signal
  byte LidarStatus=0;
  if (not digitalRead(PIN_LIDAR_WARNING)) bitSet(LidarStatus,0); 
  if (not digitalRead(PIN_LIDAR_PROTECT)) bitSet(LidarStatus,1); 
  if (not digitalRead(PIN_LIDAR_DIRTY)) bitSet(LidarStatus,2); 
  return(LidarStatus); 
}

void ResetLidar (){
  //Sends a pulse for resetting Lidar
  digitalWrite(PIN_LIDAR_RESET, HIGH);
  delay(10);
  digitalWrite(PIN_LIDAR_RESET, LOW);
}

void SetMotorsVelocity(float Linear_Velocity, float Angular_Velocity) {
  //Set Motors_setpoint and Motors_deviation based on the inputs: Speed in meters/second (-MOTORS_MaxLinear_Velocity to MOTORS_MaxLinear_Velocity) 
  //and Rotation in radians/second (-MOTORS_MaxAngular_Velocity to MOTORS_MaxAngular_Velocity)

  int16_t Motors_deviation = 0;             //Direction of AMR. negative turns to the left, positive turns to the right. Same units as Motors_setpoint

  //Control limits
  if (Linear_Velocity  < -MOTORS_MaxLinear_Velocity) Linear_Velocity  = -MOTORS_MaxLinear_Velocity;
  if (Linear_Velocity  >  MOTORS_MaxLinear_Velocity) Linear_Velocity  =  MOTORS_MaxLinear_Velocity;
  if (Angular_Velocity < -MOTORS_MaxAngular_Velocity) Angular_Velocity = -MOTORS_MaxAngular_Velocity;
  if (Angular_Velocity >  MOTORS_MaxAngular_Velocity) Angular_Velocity =  MOTORS_MaxAngular_Velocity;

 // if ((Linear_Velocity > -0.15) and (Linear_Velocity < 0.15)) Linear_Velocity = 0.0; //range between -0.099 and 0.099 is considered as 0

  Motors_setpoint = Linear_Velocity * PID_Interrupt_ms * 12.875;
  /*  How is this formula defined:
   *  
   *  Initial constants:
   *  -encoder CPR: 200CPR (cycles per revolution in motor axel)
   *  -gear ratio of motors: 103/4
   *  -CPR_on_wheel (Resulting cycles per revolution in wheel axel): encoder CPR * gear ratio = 5150 cycles per revolution of wheel
   *  -Diameter of wheel: 130mm = 13cm = 0.13m
   *  -Perimeter_of_wheels_in_meters: Pi * Diameter = 0.4m
   *  -1 minute = 60000ms
   *  
   *  Motors_setpoint is measured in cycles of encoder per measuring time (PID_Interrupt_ms)
   *  
   *  
   *  Speed_meters_per_minute = Linear_Velocity(m/s) * 60 seconds
   *  revolutions_per_minute = Speed_meters_per_minute / Perimeter_of_wheels_in_meters = Linear_Velocity * 60 / 0.4 = Linear_Velocity * 150
   *  revolutions_per_ms = revolutions_per_minute / 60000 = (Linear_Velocity * 150) / 60000 = Linear_Velocity * 0,0025
   *  
   *  Motors_setpoint = revolutions_per_ms * PID_Interrupt_ms * CPR_on_wheel = (Linear_Velocity * 0,0025) * PID_Interrupt_ms * 5150 = Linear_Velocity * PID_Interrupt_ms * 12,875
   */

  Motors_deviation = Angular_Velocity * PID_Interrupt_ms * 0.836875; 
  /*  
   *  linear speed = angular speed x radius of the rotation
   *  v = ωr
   *  v = linear speed (m/s)
   *  ω = angular speed (radians/s)
   *  r = radius of the rotation (m)
   *  
   *  Then:
   *  Distance between wheels (L): 325mm = 32,5cm = 0.325m
   *  Radius_of_rotation (L/2) = 0.065m, because the centre of rotation (T) is in the middle of the robot.
   *  Linear Speed on the wheel (v) = Angular_Velocity (ωp) * Radius_of_rotation (L/2)
   *  
   *  This Linear Speed should be applied in positive to one wheel and in negative to the other (differential drive) 
   *  not altering the linear velocity of the robot (Linear_Velocity) defined in the previous page. 
   *  To apply it properly we need to add and subtract to Motors_Setpoint but in the same units, 
   *  so we need to apply to the Linear Speed on the wheel the same conversion we did previously 
   *  for Linear Velocity getting Motors_deviation:
   *  
   *  Motors_deviation = Linear Speed on the wheel (m/s) * PID_Interrupt_ms * 12,875 =
   *  (Angular_Velocity(r/s) * Radius_of_rotation) * PID_Interrupt_ms * 12,875
   *  (Angular_Velocity(r/s) * 0.065m) * PID_Interrupt_ms * 12,875 =
   *  Angular_Velocity * PID_Interrupt_ms * 0,836875
   *  
   *  Then we add and subtract to Motors_setpoint (VT) of each wheel getting Motor1_Setpoint (VR) and Motor2_Setpoint (VL)
   */

  Motor1_setpoint = Motors_setpoint - Motors_deviation;
  Motor2_setpoint = Motors_setpoint + Motors_deviation;

}

  
void SetLidarCase(byte cases) {
  //Set Lidar Cases (0:Short case, 1:Long case, 2:Park mode, 3:No detection) 
  digitalWrite(PIN_LIDAR_CASEBIT0, bitRead(cases, 0));
  digitalWrite(PIN_LIDAR_CASEBIT1, bitRead(cases, 1));
}
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
void loop() { 

  //ROS integration
  ROSpub_t2 = millis();
  if (ROSpub_t2 - ROSpub_t1 > ROSpub_t_interval) {
    ROSpub_t1 = ROSpub_t2;
    
    //Velocity messages
    velocity_lin_msg.data = Global_Linear_Velocity;
    velocity_ang_msg.data = Global_Angular_Velocity;
    pub_velocity_lin.publish( &velocity_lin_msg );
    pub_velocity_ang.publish( &velocity_ang_msg );

    //Safety message
    safety_status_msg.data = 0;
    if (bitRead(LidarCase, 0))              bitSet(safety_status_msg.data,0); //Lidar case
    if (bitRead(LidarCase, 1))              bitSet(safety_status_msg.data,1); //Lidar case
    if (not digitalRead(PIN_LIDAR_WARNING)) bitSet(safety_status_msg.data,2); //Lidar warning
    if (not digitalRead(PIN_LIDAR_PROTECT)) bitSet(safety_status_msg.data,3); //Lidar protective
    if (not digitalRead(PIN_LIDAR_DIRTY))   bitSet(safety_status_msg.data,4); //Lidar dirty
    if (digitalRead(PIN_SAFETYSTOP))        bitSet(safety_status_msg.data,5); //Safety stop (from Safety PLC)
    if (digitalRead(PIN_BUTTON))            bitSet(safety_status_msg.data,6); //Button pressed
    pub_safety_status.publish( &safety_status_msg );
    
    //RFID message
    strcpy(rfidcode, RFID_read.tag.c_str()); // copying the contents of the string to char array
    rfid_tag_msg.data = rfidcode; //Last RFID value read
    pub_rfid_tag.publish( &rfid_tag_msg );
    
    nh.spinOnce();
  }
  

  //Check if any key from membrane keypad is pressed
  customKey = customKeypad.getKey();  
  if (customKey) KbdKey = customKey;  

  //After booting, the Lidar Scanner needs 20 seconds to be ready
  if (not Lidar_ready) {
    uptime::calculateUptime();
    if (uptime::getSeconds() > 20) Lidar_ready = true;
  }
  
  if (Buzzer_warnings_allowed) Buzzer_warnings(); //Check if there are warning conditions and inform users via buzzer

  HMI_update(); //Check keys pressed and update LCD screen (Human-Machine interface) every LCD_t_interval msec
  
  if (MagGuidance_Active) MagGuidance();   //Mag Guidance

  if (RFID_Active) RFID_Actions(); //Check if RFID interrogator detects any RFID tag

  //ExtCmds_Actions(); //Checks if external commands comming via serial <<<<----- commented as it interfere with Rosserial, as flushes the same serial buffer used to keep communication between HLC and LLC

  //General Purpose button at the back of the AMR
  if (digitalRead(PIN_BUTTON)==true) digitalWrite(PIN_BUTTON_LED, HIGH); //If button is pressed, switch on its led
  else                               digitalWrite(PIN_BUTTON_LED, LOW);  //Otherwise, switch it off

  //Motors STOP conditions
  if (digitalRead(PIN_SAFETYSTOP) or set_stop) {                 //Safety Stop active or set_stop activated  (Drives are off. We need to stop PIDs to prevent overshooting)
    Motors_active_status = false; //Condition to stop motors
    Motor1_PID.clear();
    Motor2_PID.clear();
    Motor1_PWM = MOTORS_PWM_STOP;
    Motor2_PWM = MOTORS_PWM_STOP;
    PID_output1 = 0; //Prevents accumulated values
    PID_output2 = 0; //Prevents accumulated values
    delay(100);
    digitalWrite(PIN_MOTORS_ACTIVE, false);   //Stop motors signal 
  } 
  else if ( Motors_active_status == false) { //Comes from a stop condition but no longer should be stopped
    digitalWrite(PIN_MOTORS_ACTIVE, true);   //Activate motors signal  
    Motors_active_status = true; //Condition to keep motors on    
  }

  //Motors speed update
  if((Global_Linear_Velocity != Global_Linear_Velocity_pre) or (Global_Angular_Velocity != Global_Angular_Velocity_pre)) {
    SetMotorsVelocity(Global_Linear_Velocity, Global_Angular_Velocity);
    Global_Linear_Velocity_pre = Global_Linear_Velocity;
    Global_Angular_Velocity_pre = Global_Angular_Velocity; 
  }


}
